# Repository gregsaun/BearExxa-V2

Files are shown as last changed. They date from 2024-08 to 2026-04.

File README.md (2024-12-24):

# BearExxa V2

## Table of contents
  1. [Introduction](#introduction)
  1. [Features](#features)
  1. [Disclaimer](#disclaimer)
  1. [Project Status](#project-status)
  1. [How To](#how-to)
  1. [Compatibility](#compatibility)
  1. [Bill Of Materials](#bill-of-materials)
  1. [Download](#download)
  1. [Print Settings](#print-settings)
  1. [Assembly Guide](#assembly-guide)
  1. [Configuration](#configuration)
  1. [Optional Parts](#optional-parts)
  1. [Official Kit](#official-kit)
  1. [Community And Help](#community-and-help)
  1. [Support My Work](#support-my-work)
  1. [Credits And Thank you](#credits-and-thank-you)
  1. [License](#license)

## Introduction 

This is the repository for the Bear EXtruder and X Axis version 2 (BearExxa V2). It improves Prusa MK2.5(S, S+) and MK3(S, S+) print quality, speed, reliability and serviceability. It's the [BearExxa V1](https://github.com/gregsaun/bear_extruder_and_x_axis) successor.

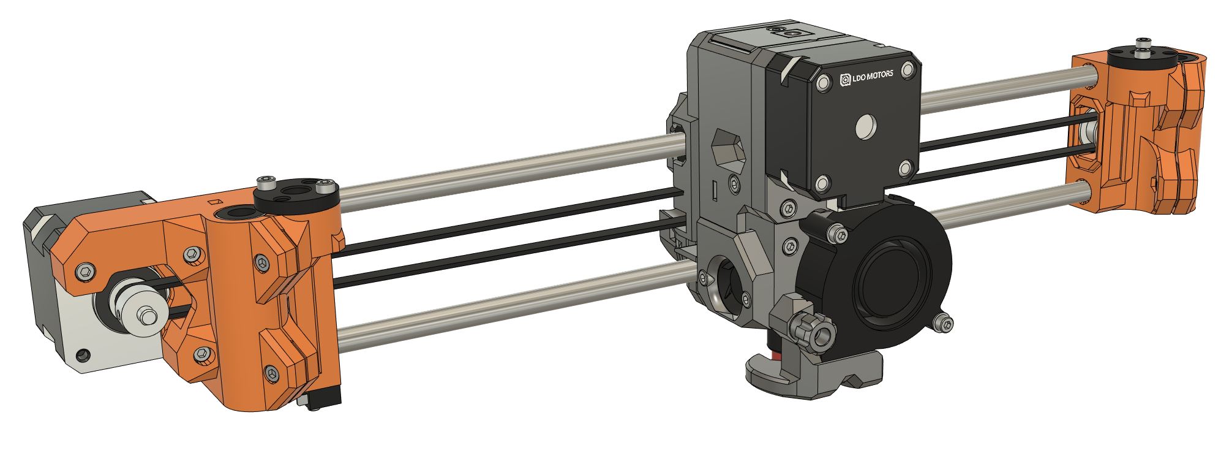
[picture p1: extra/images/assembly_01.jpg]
BearExxa V2 CAD assemnly


## Features

  - Compatible with stock Prusa MK2.5(S, S+) and MK3(S, S+) hardware as well as Bear frame
  - High print quality by solving both repetitive and random extrusion artifacts. Read our [Design Goals](extra/design_goals.md) for more information
  - High torque and cold extruder motor for the best reliability and print quality in all conditions
  - Light print head without compromising features
  - Short filament path
  - Built-in filament sensor
  - Very concentric extruder gearing
  - Stiffer X axis
  - Efficient belt tensioning system
  - E3D Revo hotend with quick swap nozzles
  - Support multicolour printing (MMU or ERCF)
  - Quick and easy to service
  - Optimized for high reliability
  - Improved cable management
  - Special attention to safety with CE compliant hardware and careful testing
  - No special tools, no crimping, no soldering and no difficult adjustments required during the assembly
  - Detailed assembly guides and documentation
  - Fully open source
 
:arrow_right: [Read our detailed Design Goals](extra/design_goals.md) to understand how we engineered those features.

## Disclaimer

This project is only to provide an alternative extruder and X axis to your Prusa printers. We are not related to Prusa Research. We cannot be taken responsible for any damages you may do by using this project nor any decision Prusa would take on you (e.g.: loosing warranty). This project is at your own risk.

## Project Status

Status: Beta 6 release done

This project is on hold for now. It's provided "as is" for any adventurous users interested in having a good extruder for their Prusa or Bear. The beta version of the BearExxa V2 provided here is fully functional and safe to use. The end goal is to provide a kit with all the parts and an improved stepper and hardware for better print quality and reliability (read our [Design Goals](extra/design_goals.md)).

## How To

How to print, build and start using the BearExxa V2:

1. Read the [Project Status](#project-status), [Disclaimer](#disclaimer) and [Compatibility](#compatibility) to make sure you agree to the limitations
2. Buy the official BearExxa v2 kit or gather the parts using the [BOM](#bill-of-materials)
3. Buy the filament according to the [Print Settings](#print-settings)
4. [Download](#download) the BearExxa V2 printed parts
5. Calibrate your filaments with our [Calibration Guide](https://guides.bear-lab.com/Guide/Extrusion+multiplier+and+filament+diameter/8)
6. Slice and print the parts according to the [Print Settings](#print-settings)
7. Follow the [Assembly Guide](#assembly-guide)
8. Enjoy your new extruder :)

## Compatibility

The BearExxa V2 is compatible with both Prusa MK2.5(S, S+) and MK3(S, S+). The original and Bear frames are both supported. The stock firmware can be used except for the initial calibration (self tests) for which we provide our own firmware.

:arrow_right: [Read all the compatibilities in details here](doc/compatibility.md)

## Bill Of Materials

The BOM includes the list of printed parts and hardware needed.

:arrow_right: [Read the BOM here](doc/bom.md)

## Download

Click here to download the printed parts for currently the recommended version (v2.0.0-beta.6):



## Print Settings

> [!WARNING]
> Follow the recommended print settings and [**calibrate your extrusion multiplier**](https://guides.bear-lab.com/Guide/Extrusion+multiplier+and+filament+diameter/8) before printing the parts.

:arrow_right: [Read the print settings here](doc/print_settings.md)

## Assembly Guide

For the current beta version we only provide a quick assembly guide.

:arrow_right: [Read the quick assembly guide here](doc/quick_assembly_guide/README.md)

## Configuration

Configurations needed for steppers and extruder values.

> [!NOTE]
> The configuration for the Original Prusa MK2.5(S, S+) and MK3(S, S+) is covered in the assembly guide.

➡️ [Find the configuration here](doc/config)

## Optional Parts

### Official optional parts

  - Multicolour with MMU or ERCF: [optional_parts/mmu_ercf](optional_parts/mmu_ercf)
  - Reverse Bowden: [optional_parts/reverse_bowden](optional_parts/reverse_bowden)
  - X-end tensioner for E3D toothed idler: [optional_parts/x_end_idler_tensioner_e3d](optional_parts/x_end_idler_tensioner_e3d)

Click here to download all optional parts (v2.0.0-beta.6):



### Community's optional parts

Find optional parts designed by the community at [guides.bear-lab.com/Wiki/community_optional_parts](https://guides.bear-lab.com/Wiki/community_optional_parts).

## Official Kit

> [!NOTE]
> The official kit is not yet available. Will be sold for the first RC release.

### What's included
  - Custom extruder motor by LDO Motors (read the [Design Goals](extra/design_goals.md) for more information)
  - Hotend fan with tachometer wire to pass Prusa firmware self tests and have extra safety
  - Quality toothed idler with dual bearings and correctly sized flanges
  - Wires and textile sleeve for a clean wiring
  - Bondtech hardware
  - All the necessary small hardware (screws, nuts, dowel pins, PTFE tube, etc.)

### What's not included
As the kit is dedicated to Original Prusa printers the kit doesn't include:
  - Z axis Lead screw nuts
  - X axis smooth rods
  - X and Z axis linear bearings
  - X axis motor
  - Filament sensor PCB, ball and magnets
  - SuperPinda (or Pinda v2)

To allow flexibility on the hotend side the kit doesn't include:
  - E3D Revo Micro heatsink
  - E3D Revo HeaterCore
  - E3D Revo nozzle

## Community And Help

- Bluesky: [@gregsaunier.bsky.social](https://bsky.app/profile/gregsaunier.bsky.social)
- Discord server "The 602 Wasteland": [discordapp.com/invite/hYUjSnW](https://discordapp.com/invite/hYUjSnW)
- GitHub: [github.com/gregsaun](https://github.com/gregsaun)
- Mastodon: [fosstodon.org/@bear_lab](https://fosstodon.org/@bear_lab)
- Patreon: [patreon.com/gregsaun](https://www.patreon.com/gregsaun)

Do not hesitate to ask if you have a question.

## Support My Work

The bear project is made possible thanks to its supporters. You can help via

- Patreon: [patreon.com/gregsaun](https://www.patreon.com/gregsaun)
- PayPal: [paypal.me/gregsaun](https://www.paypal.me/gregsaun)
- GitHub Sponsor: [github.com/sponsors/gregsaun](https://github.com/sponsors/gregsaun)

Massive thank you in advance :heart:

## Credits And Thank You

- The close help of Florian Däubler, [Paul_GD](https://github.com/PaulGD03), [Schaun Doe](https://www.printables.com/@ShaunDoe), Sleene and  [vertigo235](https://www.printables.com/@vertigo235_33)
- All [my Patreons](https://www.patreon.com/gregsaun), it would have been impossible without their help
- [LDO Motors](https://ldomotors.com) for their continuous and precious support and sponsoring. LDO will manufacture the official kit for the final release with a custom stepper
- [E3D Online](https://e3d-online.com) for providing free hotends for development
- [Bondtech](https://www.bondtech.se) for providing free IDGA gears for development
- The [fan duct knob](https://www.printables.com/model/113157-bear-extruder-v1-fan-duct-knob) by Amelia Marie Collins
- [René Jurack](https://rene-jurack.de) for helping me on CFD simulation for the nozzle fan duct
- [Credits from BearExxa V1](https://github.com/gregsaun/bear_extruder_and_x_axis?tab=readme-ov-file#credit-and-inspiration) related to X Ends: Vecko Kojchevski, Arnaud Rousseau and Jon Madden
- Keith Bennett for making the [Prusa AIO firmware](https://github.com/thisiskeithb/PrusaAIO) compatible
- [PoiTEE](https://x.com/PoiTEE) for the great talks and testing
- [FilamentFrenzy](https://x.com/FilamentFrenzy) for having tested and make noise for an early version
- Prusa Research for their MK2.5S and MK3S designs
- Adrian Bowyer for inventing [RepRap](https://reprap.org)

Thank you everyone ❤️

## License

The Bear EXtruder and X Axis v2 (BearExxa V2) is an open-source hardware project created from scratch by Grégoire Saunier with help and inspiration from the people and companies listed under "Credits and Thank You" as well as contributions linked to this repository.

All texts, images, PDF files and animations in this repository are licensed under the terms of the CC-BY-SA 4.0 license. The full license text of CC-BY-SA 4.0 is available in this repository at [`./LICENSE-CC-BY-SA-4.0`](./LICENSE-CC-BY-SA-4.0). Read more about this license [here](https://creativecommons.org/licenses/by-sa/4.0/).

All G-code files in this repository are licensed under the terms of the MIT license. The full license text of MIT is available in this repository at [`./LICENSE-MIT`](./LICENSE-MIT). Read more about this license [here](https://opensource.org/license/MIT).

All content in this repository, except for texts, images, PDF files, animations and G-code files is licensed under the terms of the CERN-OHL-P v2 license. The full license text of CERN-OHL-P v2 is available in this repository at [`./LICENSE`](./LICENSE). Read more about this license [here](https://cern-ohl.web.cern.ch/).

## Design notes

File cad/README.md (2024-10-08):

# BearExxa V2

## CAD

> [!IMPORTANT]
>The X end idler and its tensioner are a working progress in these CAD files. They are **currently** not compatible with the previous X end idler and tensioner. The STL files exported into `../printed_parts/stl` are a copy of the Bear extruder V1 X ends ([source files of V1](https://github.com/gregsaun/bear_extruder_and_x_axis/tree/master/source)). The future revisions will make them compatible with the V1.

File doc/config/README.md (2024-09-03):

# BearExxa V2

## Configuration

### Original Prusa MK2.5(S, S+) and MK3(S, S+)

Due to the gear ratio of the BearExxa V2 we need to configure the estep and microstepping values.

➡️ [Download the config files `prusa_original/config_prusa_original_bearexxav2_beta.zip`](./prusa_original/config_prusa_original_bearexxav2_beta.zip).

In the ZIP you will find the following files:
  * `bearexxa2_config.gcode`: Use this file to setup microstepping and estep.
  * `reset_config_to_prusa_mk2.5-2.5s-3-3s.gcode`: Use this file to reset changes previously applied for BearExxa v2 to stock Prusa config.

### Prusa AIO firmware (Marlin 2.x)

*to do*

### Klipper

*to do*

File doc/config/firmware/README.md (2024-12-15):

# BearExxa V2

## Firmware Configuration

### Table of Contents

  1. [Original Prusa MK2.5(S, S+) and MK3(S, S+)](#original-prusa-mk25s-s-and-mk3s-s)
  1. [Prusa AIO firmware (Marlin 2.x)](#prusa-aio-firmware-marlin-2x)
  1. [Klipper](#klipper)
  1. [Generic](#generic)

### Original Prusa MK2.5(S, S+) and MK3(S, S+)

Due to the gear ratio of the BearExxa V2 we need to configure the estep and microstepping values.

In the folder [prusa_original](prusa_original) you will find the following files:
  - `bearexxa2_config.gcode`: Use this file to setup microstepping and estep.
  - `reset_config_to_prusa_mk2.5-2.5s-3-3s.gcode`: Use this file to reset changes previously applied for BearExxa v2 to stock Prusa config.

> [!WARNING]
> These GCODE files only applyto Prusa firmware and **not** to Prusa AIO or Klipper.

### Prusa AIO firmware (Marlin 2.x)

BearExya V2 is officially supported by the Prusa AIO firmware. Please refer to the [GitHub](https://github.com/thisiskeithb/PrusaAIO) and [wiki](https://github.com/thisiskeithb/PrusaAIO/wiki) for the configuration.

### Klipper

#### Extruder
```yaml
[extruder]
rotation_distance: 22.616
microsteps: 32
full_steps_per_rotation: 200
gear_ratio: 2.94:1
sensor_type: ATC Semitec 104NT-4-R025H42G
```
> [!WARNING]
> These are not complete configurations. Please adjust your configuration to reflect the values below.

#### Extruder motor driver
For TMC2209 and TMC2130 using the Klipper extension  [klipper_tmc_autotune](https://github.com/andrewmcgr/klipper_tmc_autotune).
```yaml
run_current: .42
```

#### X axis motor driver
For TMC2209 and TMC2130 using the Klipper extension  [klipper_tmc_autotune](https://github.com/andrewmcgr/klipper_tmc_autotune).
```yaml
run_current: .5
```
> [!NOTE]
> Using the TMC Autotune extension is not a requirement, and these motor currents are only a recommendation.
> 
> Please adjust these values according to the motors you are using, ideally >50% and <80% of the rated current.

### Generic

#### Extruder

```
Number of steps per motor rotation: 200
Microsteps: 32
Gear Ratio: 2.94:1
Effective hobb gear diameter: 7.22mm
Running current: 420mA RMS
Holding current: 420mA RMS
Interpolation: true
Hotend thermistor: Semitec 104NT-4-R025H42G 
```

#### X axis

```
Number of steps per motor rotation: 200
Microsteps: 16
Running current: 500mA RMS
Holding current: 300mA RMS
Interpolation: true
 ```

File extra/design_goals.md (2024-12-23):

# BearExxa V2

## Design Goals

### Table of contents

1. [Introduction](#introduction)
1. [Print quality](#print-quality)
1. [Reliability](#reliability)
1. [Weight, rigidity and speed](#weight-rigidity-and-speed)
1. [Custom extruder motor](#custom-extruder-motor)
1. [Serviceability and maintenance](#serviceability-and-maintenance)
1. [Safety](#safety)
1. [FAQ](#faq)

### Introduction

The main goals of the BearExxa V2 are to use a better hotend and geared extruder to improve the print quality, reliability, serviceability, precision, speed and to solve inconsistent extrusion issue (602 issue).

There are several ways to achieve this and it's a question of what compromises you do and how you test things. In this page we describe our design process and the goals we have set to achieve the BearExxa V2.

BearExxa V2 assembly

### Print quality

This extruder improves print quality by using a geared extruder, a well engineered hotend and several thoroughly designed features. Here is how we have cured the 602 issue (inconsistent extrusion issue) as well as improving even further the print quality:

#### Random extrusion artifacts and precision

The first crucial aspect to get quality prints is to handle the filament precisely and rigidly down to the melt zone.

To achieve this we use a perfectly aligned, short and smooth filament path to reduce any potential friction. The path is shorter than on the original MK3(S, S+).

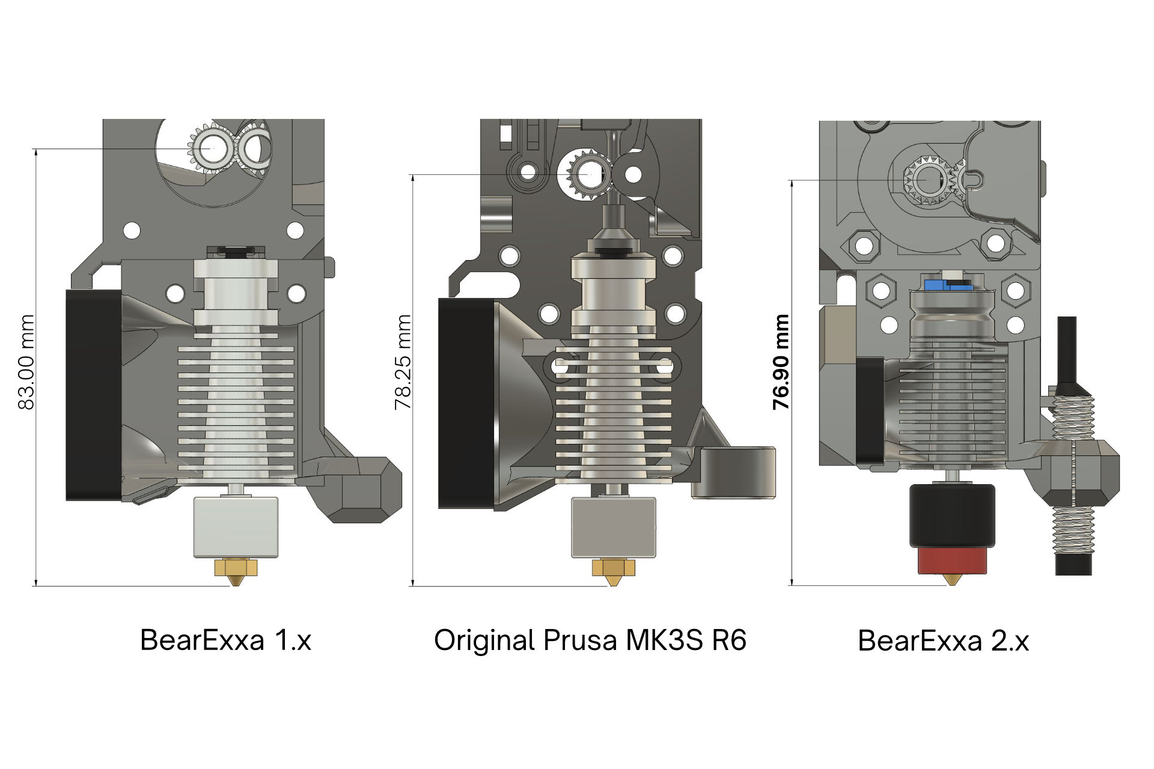
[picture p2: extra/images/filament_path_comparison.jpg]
BearExxa V2 filament path length comparison


We use a NEMA 17 pancake motor to keep the hobb gears and its cavity as cold as possible, even on long PLA prints in enclosure with doors closed. This helps to keep the filament as rigid as possible before the hotend and so increase precision.

We are also using the small set of the dual Bondtech hobb gears as its small diameter allows to catch the filament exiting the hobb gears closer than with a larger diameter. It reduces chances for the filament to go out of the path like it could happen with flexible filaments.

Then comes the hotend, we chose the E3D Revo because we have observed that it's particularly good at reducing random artifacts on perimeters compared to some competitors we have evaluated or tested. But it needs a good control of the filament on both cold and hot sides, so we took care of the airflow and thermal management to get a very sharp thermal transition in the heatbreak. This is achieved with the Revo Micro heatsink, a properly sized fan and a careful aiflow's management.

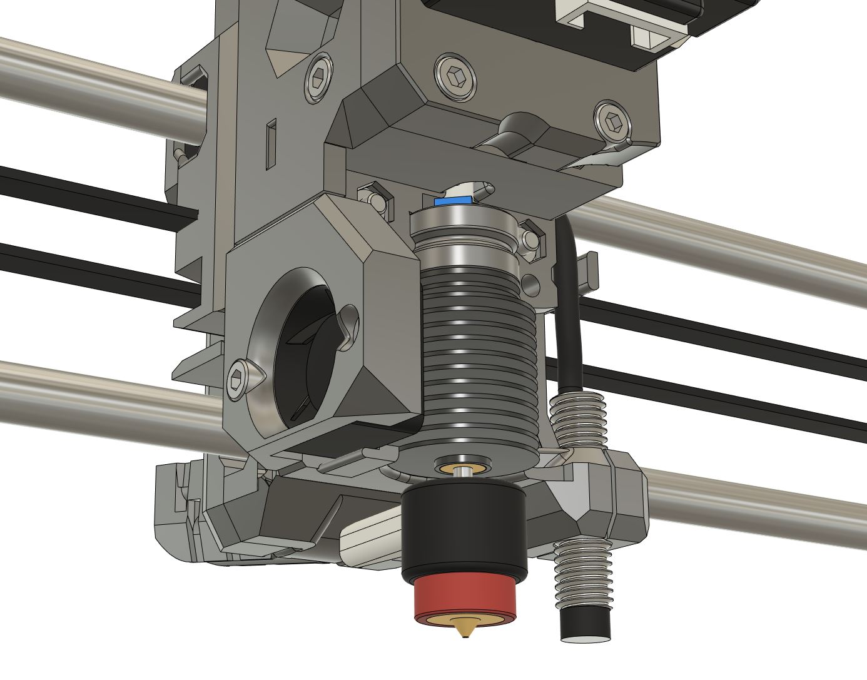
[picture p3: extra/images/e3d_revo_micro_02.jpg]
BearExxa V2 Hotend and its fan


Furthermore, we made sure to have a free space right below the heatsink to cool this side as well with the movements of the tool head. It's important because the bottom side of the heatsink is where it matter the most for the heatbreak.

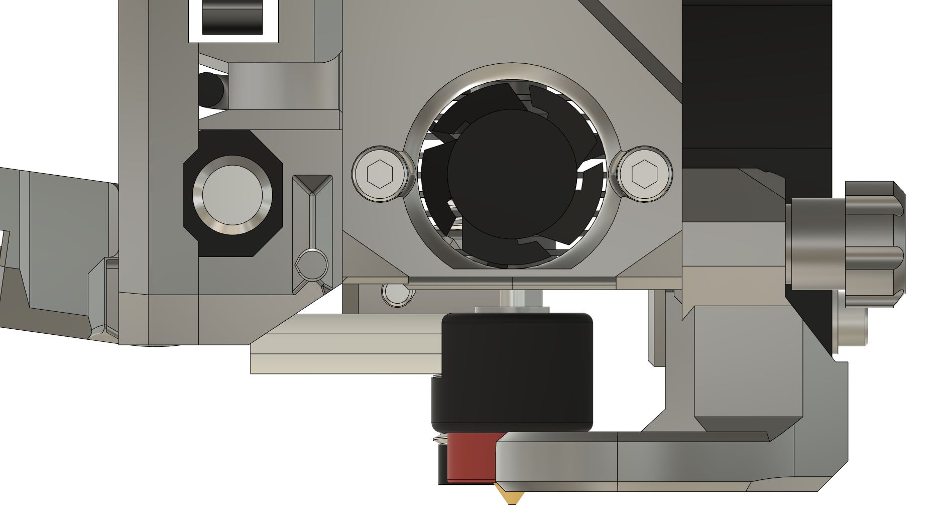
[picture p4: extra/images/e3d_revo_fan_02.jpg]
BearExxa V2 hotend cooling


All these features **improve random extrusion artifacts and increase the accuracy** of your prints.

#### Repetitive extrusion artifacts

The extruder uses a gear ratio of 3:1 (with beta release) or almost 4:1 (with the future final release). 

We took care of using appropriate teeth numbers to have a smooth rotation and to reduce the wear on the teeth (e.g. coprime number of teeth, hardened teeth, large surface of contact). We believe that the print quality should be the same even after many hours of use!

The custom motor has enough torque to not make the motor's steps more visible when the pressure increases in the hotend due to non-optimal settings or other small issues (wider extrusion, partial clog, too high flow rate, ...). This custom motor has a very concentric gear that will reduce variations in the rotation. For the final release we are also planning to use the all in one piece Bondtech shaft and hobb gear (IDGA) to once again reduce the variations.

All those features **improve the so called "moiré pattern" (also called basket wave or wood grain pattern)** or, in other words, the repetitive extrusion artifacts.

#### Single vs dual hobb gears

Finally, we have made several tests comparing single vs dual gears and we couldn't see a difference. We also asked the Bear community to test on their side and they had the same conclusion.

We understand there is a gear meshing issue but we think it can potentially only happen during retraction or maybe the artifacts are too small to be visible.

We also think that some of our design decisions are potentially helping to minimise this issue (rigid extruder cavity, tight tolerances to align the gears, good amount of tension with visible indicator, precise filament path, etc.).

We may later provide a mod to use a single gear for making your own conclusion. We are keeping an eye on this topic and for now we haven't seen good enough testing proving there is a noticeable difference.

### Reliability

Reliability is a strong goal of this extruder. We use a NEMA 17 pancake motor to keep the hobb gears and the extruder cavity as cold as possible during extensive PLA prints in enclosure (door closed).

After multiple testing with belts and planetary gearboxes we found that a single stage of spur gears is the best compromise. It's light, easy to assemble and has a very low part count, which means less parts can fail.

We use the Bondtech gear shaft and hobb gears, but we replaced the original bearings by larger ones to increase lifespan (and smoothness).

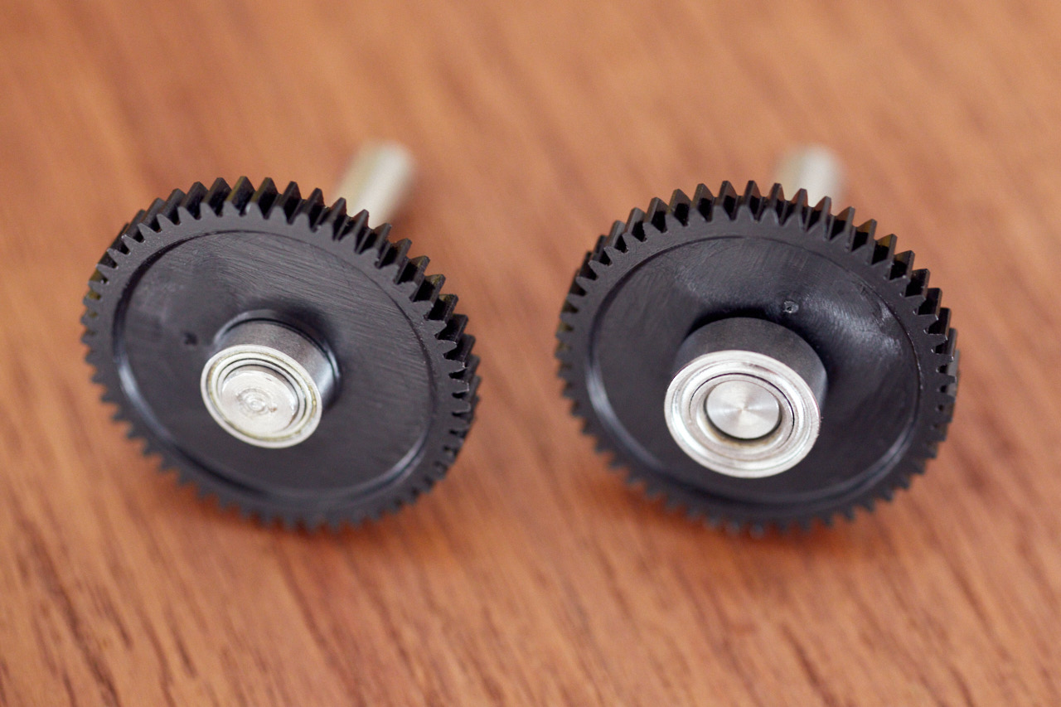
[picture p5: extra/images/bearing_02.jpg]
BearExxa V2 bearings


We use the E3D Revo Micro hotend for its professional support and compliances with worldwide regulations. We optimized the hotend airflow for the best heatbreak performance possible, low noise and to avoid grabbing tiny hairs (strings).

We placed the nozzle fan blower in vertical to maximise the lifespan of its bearings, to not get warmer air when the extruder is close to the bed and, once again, to avoid getting strings in the fan blades.

Unlike the Original Prusa MK3S and MK3S+ extruder, the filament path is in one piece to avoid a potential misalignment during assembly that would affect its smoothness. It's also shorter than the original Prusa extruder.

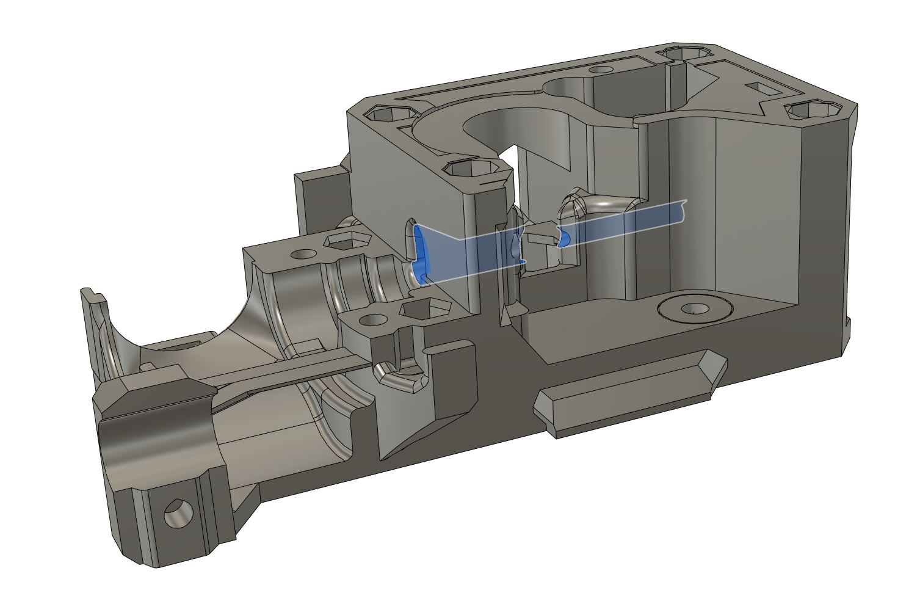
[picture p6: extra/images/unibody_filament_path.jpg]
BearExxa V2 unibody filament path


Every printed parts and features have been tested carefully. When rigidity or brittleness could be affected we made internal reinforcements within the infill to reduce any risks.

We also make sure that no special adjustments or tools are required during the assembly and maintenance. With the final release we will provide detailed assembly guide, as we always do, to avoid any potential assembly issues.

### Weight, rigidity and speed

Despite a larger motor than what's commonly used these days, a lot of work have been implemented to make the extruder as light as possible, even lighter than some extruders widely used in the community! Let's dive into how we achieved this.

First, it's important to remember that a bed slinger printer doesn't have to carry the weight of the gantry like on a CoreXY machine, which means the mass in motion is lighter than we could first think. However, obviously, the bed is heavier and will be the bottleneck.

On our design, we reduced the weight by using a light and small hotend (including the fan), using a single stage spur gears instead of a heavier planetary gearbox, lowering the number of screws, using small hobb gears, carefully selecting the hardware, not adding extra useless features and designing a compact body.

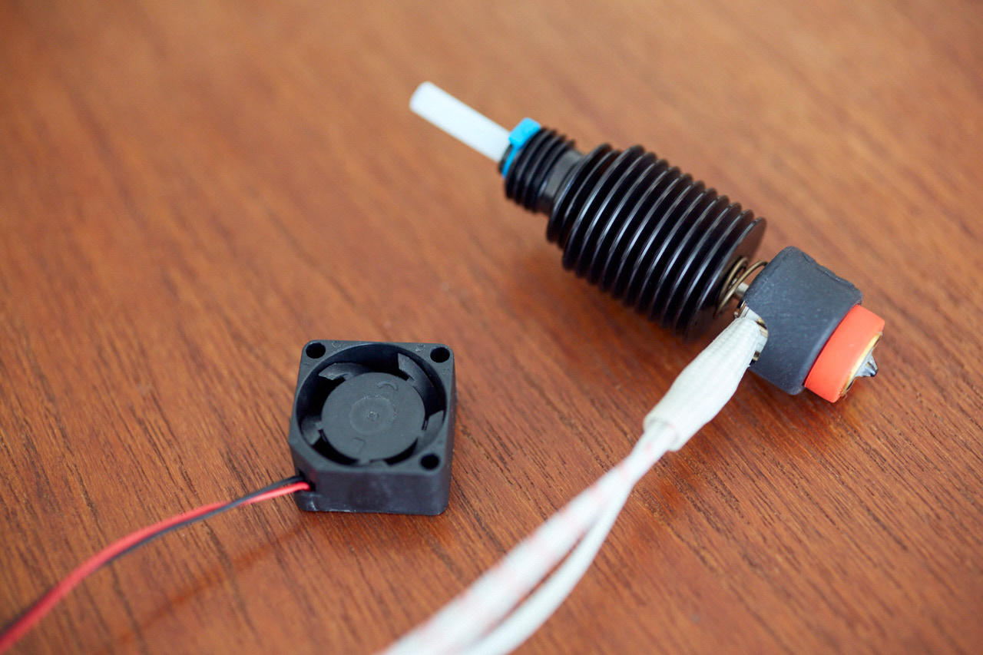
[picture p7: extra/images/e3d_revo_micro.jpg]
E3D Revo Micro and its fan


As you can see we took care of every weight reduction that matters but we didn't stop there. The X axis is stiffer thanks to several design startegies: we use clamps on the Z axis bearings, X motor is closer to the Z axis, the belt tensioner is stiff and we optimized how deep the smooth rods are inserted in the X ends.

### Custom extruder motor

> [!WARNING]
> Not for the Beta release, will only be for RC and final releases.

The final release will use a custom extruder motor by LDO Motors. It was a difficult choice to take as we want to be as open hardware as possible but the improvements are significant.

This custom motor uses a carefully selected gear ratio (almost 4:1) for smoother print quality and to minimise the teeth wear (e.g. coprime number of teeth, hardened teeth, large surface of contact). It has a special construction to make the motor gear very concentric and so to reduce extrusion variations. It also helps to reduce the total weight.

The back of the motor is almost empty inside, it has been made thicker to accommodate a connector. Like this, we reduce the maintenance time and so be quicker to restart printing.

Finally, the motor specs are optimized for original Prusa printers to provide a safe amount of torque on all occasions as well as keeping the motor cold for long PLA prints in enclosure. We chose a motor that has just enough torque to grind the filament in case of a blockage. This is to avoid problems where the spool or the filament path has lots of friction (didn't we all have a failed print due to this?), to fight slightly non-optimal settings that could force on the hotend's flow, to resolve a small heat creep and to ensure manufacturing tolerances are covered (including the precision of your printed parts). With higher torque we could also imagine to later automate things like cold pulls. We believe that a finished print is always better than a failed one that will be sent to trash (even if the quality is a bit below what you wanted to achieve), so high torque was a crucial feature for us.

### Serviceability and maintenance

Thanks to the E3D Revo ecosystem you can swap nozzles with two fingers in a few seconds. And to make this even easier, you can remove the hotend fan duct with a thumb screw.

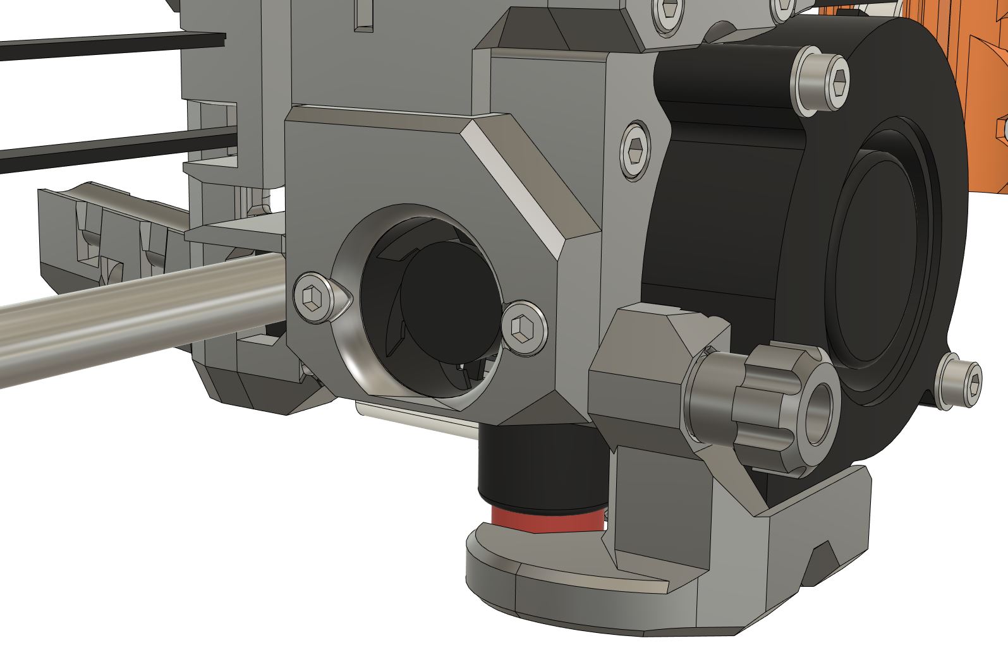
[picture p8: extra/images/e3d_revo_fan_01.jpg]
BearExxaV2 Thumb screw nozzle fan duct shroud


The hobb gear tension has a visual adjustment for the nominal tension.

The belt tensioner is easy to use and has a long adjustment range.

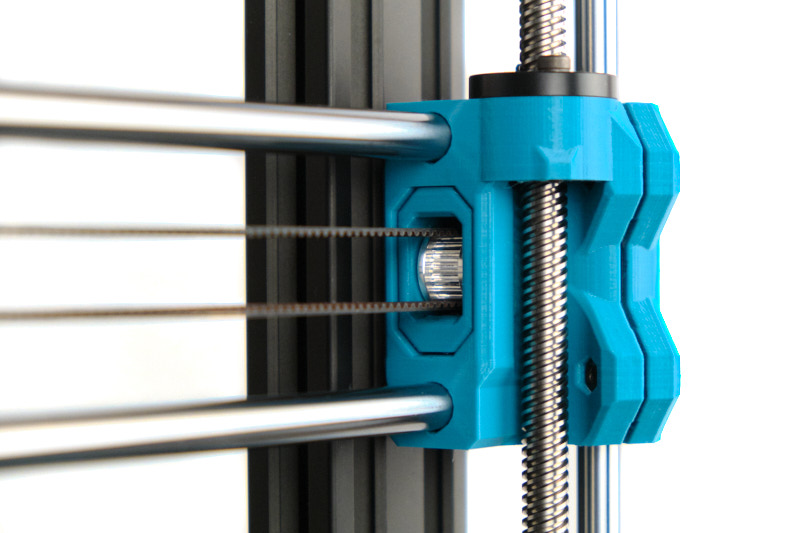
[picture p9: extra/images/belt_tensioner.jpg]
BearExxa V2 belt tensioner


You only need to remove 4 screws and unplug the motor cable to access the gearing, the hobb gears, the filament sensor and the top of the PTFE tube. Cleaning and maintenance are a breeze and quick.

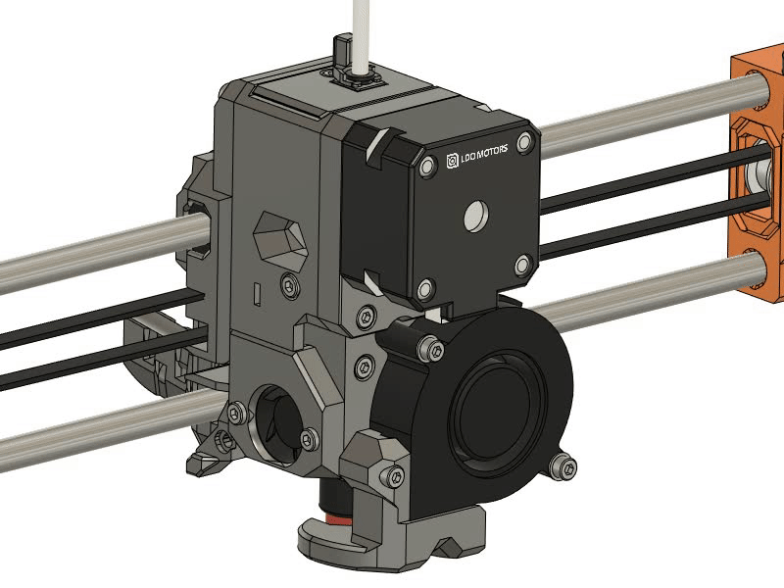
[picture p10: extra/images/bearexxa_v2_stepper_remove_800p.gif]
BearExxa V2 removing motor anf gears


We invented a self tightening groove mount that blocks the rotation of the Revo Micro heatsink thread. Like this there are zero chances to unscrew the heatsink when swapping nozzles.

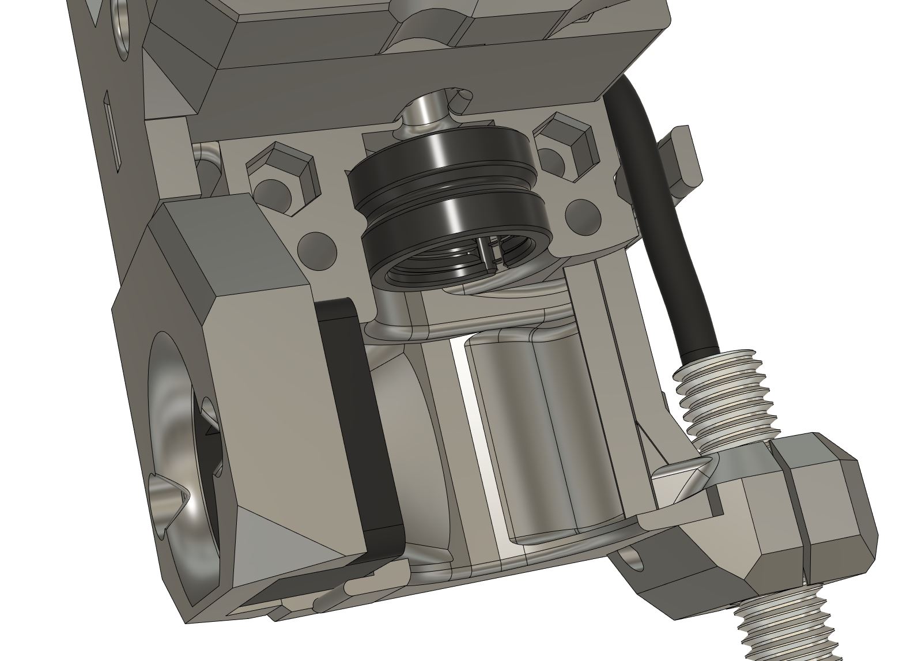
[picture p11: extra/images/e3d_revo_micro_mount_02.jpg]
E3D Revo self tightening groove mount


The back of the X carriage is made into two parts to access all the wiring and the belt freely.

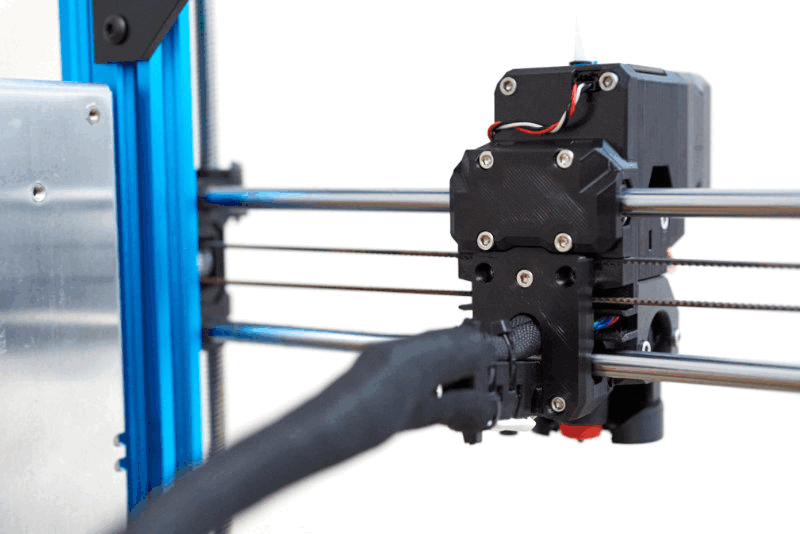
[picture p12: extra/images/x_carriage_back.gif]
BearExxa V2 X carriage back


### Safety

We can be very picky when it comes to the safety of our project, especially as it's DIY and open source. A 3D printer is a machine melting flammable plastic for hours and hours, it must be safe!

We chose the E3D Revo hotend for its worldwide compliances (CE, UKCA RoHS, etc.). It's also particularly interesting that the  Revo is using a PTC heater which offers an extra safety in case of thermal runaway. Our design ensure that the wire harness of the HeaterCore is kept straight and that no wires have sharp angle. No crimping, cutting or soldering is required. The hotend fan that will come with the final kit will have the tachometer wire to detect a fan failure.

We recommend PETG for the extruder parts because its a safe filament to use. It doesn't burn easily and do not release too much nasty fumes. The extruder has obviously been tested to support the temperature for long prints.

We provide detailed documentation, assembly guides and many other helps. Like this you reduce as much as possible the issues during assembly, printing, maintenance and have many resources in case of problems. If it's not enough we are here to provide support, there are no bad questions.

We only recommend genuine Bondtech, E3D, LDO Motors, and Prusa hardware for the best safety and support possible. We will provide an official kit that has been carefully designed and controlled (manufactured by LDO Motors). Using clone parts from another manufacturer is a risk of incompatibility, reliablitiy, legality and even fire.

### FAQ

#### Why don't you use heat inserts?
Hex or square nuts have a stronger pulling resistance than heat insert. We use carefully selected clearances to make sure the hex nuts will not move from their pocket. The nuts also take less place than heat insert. We can also simulate a lock nut by making the screw hole in the plastic a little bit smaller. It's easier to remove them from an older part to transfer them to a new one. Finally, no special tool is required.

#### Why the nozzle fan blower is in vertical and not angled like Prusa does?
It's to increase the lifespan of its bearings, to not get warmer air when we are close to the bed and to not grab strings with the fan blades. The nozzle fan duct is optimized for the 90° angle and perform better than the Original MK3(S, S+) according to our tests.

#### Why do you recommend PETG for the parts?
PETG has an excellent layer bonding, is easy to print, has high precision due to low shrinkage, is kind of semi fire retardant and produces less nasty fumes than styrene based filaments. Its temperature resistance is more toward printing PLA or PETG parts (even in enclosure) which are the most used filaments in the community. If you are an advanced user that want to print higher temperature material we recommend to use ABS, ASA or PC (and compensate for the shrinkage).

> [!CAUTION]
> We highly recommend to avoid high flow filaments (worse material properties as non high flow) as well as glass fiber or carbon fiber filaments ([potentially carcinogenic](https://hackaday.com/2024/08/07/on-carbon-fiber-types-and-their-carcinogenic-risks/)). You must ventilate your room and filter your enclosure (HEPA + activated carbon) if you print styrene based filament like ABS, ASA or PC.

#### Why don't you use a smaller extruder motor?
We have explained the reason in details in the sections "Print quality", "Reliability" and "Weight, rigidity and speed".

The extra weight is compensated by other lighter parts, low hardware count and an overall compact design. Also, it would be very hard to see a print quality improvement with a lighter motor because, on a bed slinger, we are only moving the extruder (unlike CoreXY which also moves the gantry) and the bed is the heaviest part. 

Furthermore, a larger motor can run colder and so improves print quality and reliability of a long PLA print in an enclosure (door closed). We can also have higher torque and increase the gears' lifespan, which both increase reliability and reduce maintenance.

#### Why do you use the Revo Micro heatsink and not the Revo Voron heatsink?
The Revo Micro heatsink has slightly more surface in contact with the airflow, especially when used with a smaller and lighter fan. The round shape is also easier to optimize for optimal airflow. The screw mount may sound like it may rotate but we did a self tightening system that avoid this to happen.

#### Why don't you officially support other hotends?
Using a single hotend allow us to optimize a lot of design's aspects like size, weight, filament path, etc. Supporting a single hotend means we can also have a more reliable testing and provide quality support. Finally, we choose E3D-Online Ltd. because their products have all the worldwide safety compliances, they provide a full ecosystem, they do deep research and engineering on how a hotend works and they have a professional support for their customers.

#### Why don't you use the Bondtech IDGA gear?
We are well aware of the IDGA benefits. We have actually talked about it with Bondtech engineers several years ago when the Bondtech Prusa extruder was introduced and more recently for the development of the IDGA. We also thought to design our own gears as we see improvements but making a custom motor was already a big step.

When we released the beta BearExxa V2, the IDGA gear was unfortunately not available and so it's not supported yet. We will make the final version compatible with BMG IDGA or OEM IDGA (we don't know which one is best yet). However, we can guarantee that even without the IDGA the print quality is a big step over BearExxa V1 and 602 pattern (moiré, wood grain. inconsistency) has been drastically reduced.

#### Would it be possible to use a stronger fan like the one on the MK4S?
Yes we want to work on this but at the moment we focus on stock Prusa MK3(S, S+) hardware.

#### Do you support MK3.5S?
We don't know yet but it might be possible. We are [looking for help](https://github.com/gregsaun/BearExxa-V2/issues/1) if you want to try the adventure.

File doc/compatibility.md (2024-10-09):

# BearExxa V2

## Compatibility

### Frame

The BearExxa V2 is compatible with both Original and Bear frames of Prusa MK2.5(S, S+) and MK3(S, S+).

### Firmware

#### Original Prusa firmware

The stock Prusa firmware is supported with the following conditions:
- Self tests and XYZ calibrations need to be done with the [Bear calibration firmware](https://github.com/bear-lab-3d/Prusa-Firmware/releases/latest). All the normal printing routines, including first layer calibrations, will work as normal with the stock Prusa firmware. Note that you can also safely use the Bear calibration firmware for printing daily
- The thermal algorithm for the hotend introduced in the very latest Prusa firmwares can sometimes cause issues with the fast Revo heating. There are commands to use the previous standard method (we provide the documentation to do it)
- For the **beta** release only: you will need to disable fan checks for prints and temporarily plug the stock hotend fan during self test procedure. The final version will be sold as a kit with a compatible fan and this will not be needed anymore

> [!IMPORTANT]
> This is the firmware we recommend for the best safeties and to keep all the functionalities provided by the Prusa firmware. We can provide full support to our customers with this firmware.

The final release of BearExxa V2 will not disable or affect any safeties from the original Prusa firmware (and same applies for the Bear calibration firmware). The E3D Revo hotend is actually providing an extra safety in case of thermal runaway compared to the E3D V6 used in the Original Prusa.

#### Other firmwares

> [!IMPORTANT]
> We can only provide limited support to these firmwares.

The BearExxa V2 is also compatible with the [Prusa AIO Marlin 2.x firmware](https://github.com/thisiskeithb/PrusaAIO). This firmware can run on some 32b boards. Thanks Keith for this impressive work!

We will provide main Klipper parameters for the final version of BearExxa V2.

### MMU and ERCF

The extruder is designed from scratch to be capable of multicolour printing with systems like Prusa MMU or ERCF.  You can find more information in the [optional parts](/README.md#optional-parts).

### BearExxa V1, BearMera and Bondtech Bear X axis

The X axis of BearExxa V1, BearMera (E3D Hemera) and Bear X axis and carriage for Prusa original Bondtech are all 100% compatible.

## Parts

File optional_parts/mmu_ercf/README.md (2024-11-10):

# BearExxa V2

## MMU ERCF adapter

### Introduction

To make your BearExxa V2 capable of printing in multicolour with Prusa MMU or [ERCF by EtteGit](https://github.com/EtteGit/EnragedRabbitProject).

The PTFE mount on the extruder is available in two options:
  - Reuse the Prusa hardware (brass insert and Festo coupling). Note that the brass insert is easy to remove in general
  - Use the E3D collet system for a lighter and the PTFE pass through system

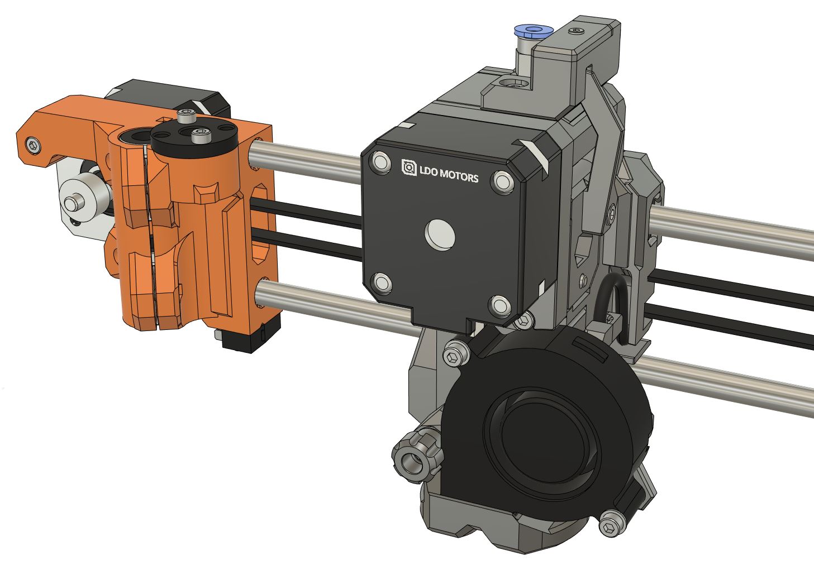
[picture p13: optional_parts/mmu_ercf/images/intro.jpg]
Introduction Bearexxa V2 MMU intro

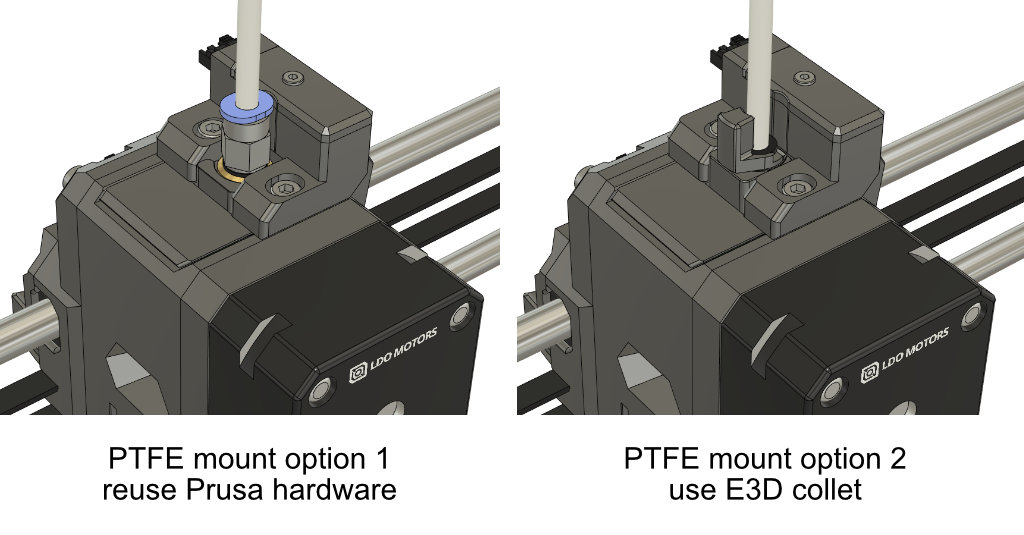
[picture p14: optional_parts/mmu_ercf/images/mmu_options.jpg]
Introduction Bearexxa V2 MMU PTFE options


### Bill of Materials

| Part | Quantity | Comment | Link |
|---|:---:|---|---|
| Prusa MMU or ERCF unit | 1 | | |
| M2x8 (ISO 4762) | 1 | | |
| M3x10 (ISO 4762) | 1 | | |
| M3x14 (ISO 4762) | 1 | | |
| M3x18 (ISO 4762) | 1 | | |
| M3 square nut (DIN 562) | 1 | | |
| M3 hex nut (ISO 4032) | 1 | | |
| E3D bowden collet for metal 1.75mm | 1 | Only for PTFE mount option 2 | [E3D link](https://e3d-online.com/products/embedded-bowden-coupling-for-metal) or [Prusa link](https://www.prusa3d.com/product/heatsink-collet/) |
| Prusa filament sensor | 1 | Comes with your Prusa MK3S (or S+) printer | [Prusa link](https://www.prusa3d.com/product/ir-filament-sensor/) |
| Prusa filament cable | 1 | Comes with your Prusa MK3S (or S+) printer | [Prusa link](https://www.prusa3d.com/product/filament-sensor-einsy-cable/) |
| Prusa 10x6x2 magnet | 1 | Comes with your Prusa MK3S (or S+) printer | [Prusa link](https://www.prusa3d.com/product/set-of-magnets-mk2-5s-mk3-s/) |
| Prusa 20x6x2 magnet | 1 | Comes with your Prusa MK3S (or S+) printer | [Prusa link](https://www.prusa3d.com/product/set-of-magnets-mk2-5s-mk3-s/) |
| Prusa 7mm steel ball | 1 | Comes with your Prusa MK3S (or S+) printer |  |

### Printed parts

Download all optional parts with the button at [Repo Homepage -> Optional Parts -> Official optional parts](/README.md#official-optional-parts)

### Print settings

> [!WARNING]
> The parts have been designed and tested with the parameters below and it is important to follow them to avoid issues like part cracking, bad bridging, not enough stiffness or wrong tolerances. You must [**calibrate your extrusion multiplier**](https://guides.bear-lab.com/Guide/Extrusion+multiplier+and+filament+diameter/8?lang=en) before printing the parts.

You can use the default PrusaSlicer print profile *0.20mm QUALITY @MK3* with 4 perimeters and 5 tops/bottoms layers and 20% infill. Otherwise, here are the parameters we recommend:

  - Slicer : PrusaSlicer
  - Nozzle size : 0.4mm
  - Layer height : 0.2mm
  - Infill : 20% Cubic or 20% Gyroid
  - Number of perimeters : 4
  - Number of top/bottom layers : 5
  - Default extrusion width : 0.45mm
  - Perimeters width : 0.45mm
  - External perimeters width : 0.45mm
  - Support : No
  - Brim : No
  - Detect thin walls : No

### Filament type

The parts are designed for PETG and this is what we recommend. Please consider recycled filament and cardboard spool or masterspool. If you are using a different filament material you will need to account for the shrinkage in XY plane directly in the slicer.

| Part | Quantity | Filament |  Color  | Comment |
|---|:---:|:---:|:---:|---|
| e_fs_adapter_mmu2s_prusa | 1 | PETG |  Any | For PTFE mount option 1 |
| e_fs_adapter_mmu2s_e3d | 1 | PETG |  Any | For PTFE mount option 2 |
| e_fs_adapter_mmu2s_e3d_clip. | 1 | PETG |  Any | For PTFE mount option 2 |
| e_fs_chimney_cover_mmu2s | 1 | PETG |  Black  | |
| e_fs_chimney_mmu2s | 1 | PETG |  Black  | |
| e_fs_cover_mmu2s | 1 | PETG |  Any | |
| e_fs_lever_mmu2s | 1 | PETG |  Black  | |
| e_tensioner_mmu2s | 1 | PETG |  Any | |

Note 1: Avoid eSUN PETG as some user reported that it might not block IR signal correctly. No other PETG have been reported to have this issue yet.

### Assembly

Read the [assembly guide here](assembly_guide/mmu_assembly_guide.pdf)

### CAD Files

The native CAD (Fusion) and STEP files are available at [`/cad/optional_parts`](/cad/optional_parts)

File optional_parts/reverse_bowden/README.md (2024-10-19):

# BearExxa V2

## Reverse bowden adapter

### Introduction

Reverse bowden has the advantage to reduce vibration and tension from the spool holder. It is also useful to guide the filament if the spool holder is not on top of the frame.

The extruder adapter is available in two options:
  - no collet where PTFE is just pushed into the hole (enough holding in most cases, easy to use and light)
  - E3D collet when strong PTFE holding is needed

The frame mount is available in two versions: standard or angled.

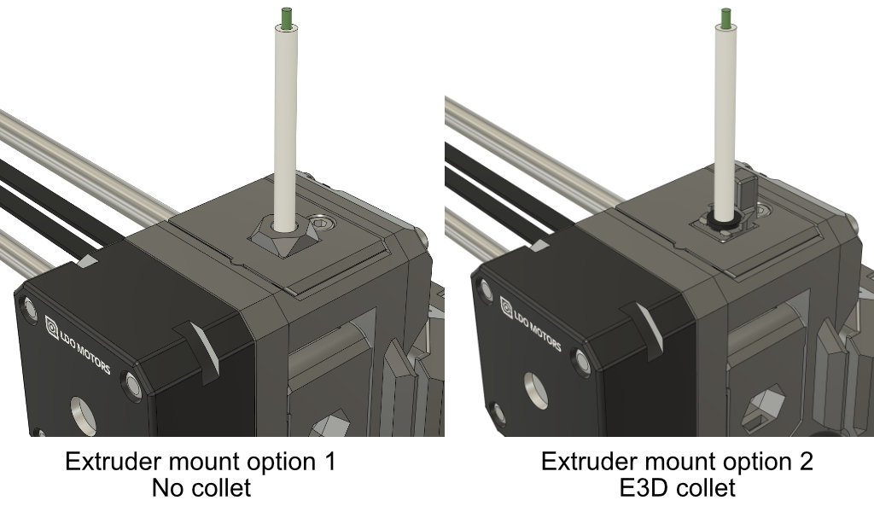
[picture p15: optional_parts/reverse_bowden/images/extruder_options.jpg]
Introduction reverse bowden

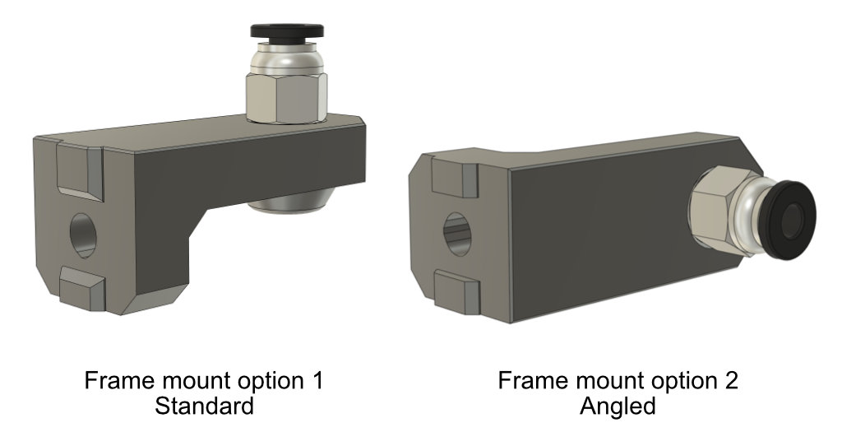
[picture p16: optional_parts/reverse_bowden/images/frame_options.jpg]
Introduction reverse bowden


### Bill of Materials

| Part | Quantity | Comment | Link |
|---|:---:|---|---|
| PTFE tube 4x2mm | 1 | | |
| E3D bowden collet for metal 1.75mm | 1 | Only for extruder option 2 | [E3D store](https://e3d-online.com/products/embedded-bowden-coupling-for-metal) |
| PC4-M10 fitting | 2 | For the frame mount |  |

### Printed parts

Download all optional parts with the button at [Repo Homepage -> Optional Parts -> Official optional parts](/README.md#official-optional-parts)

## Print settings

> [!WARNING]
> The parts have been designed and tested with the parameters below and it is important to follow them to avoid issues like part cracking, bad bridging, not enough stiffness or wrong tolerances. You must [**calibrate your extrusion multiplier**](https://guides.bear-lab.com/Guide/Extrusion+multiplier+and+filament+diameter/8?lang=en) before printing the parts.

You can use the default PrusaSlicer print profile *0.20mm QUALITY @MK3* with 4 perimeters and 5 tops/bottoms layers and 20% infill. Otherwise, here are the parameters we recommend:

  - Slicer : PrusaSlicer
  - Nozzle size : 0.4mm
  - Layer height : 0.2mm
  - Infill : 20% Cubic or 20% Gyroid
  - Number of perimeters : 4
  - Number of top/bottom layers : 5
  - Default extrusion width : 0.45mm
  - Perimeters width : 0.45mm
  - External perimeters width : 0.45mm
  - Support : No
  - Brim : No
  - Detect thin walls : No

### Filament type

The parts are designed for PETG and this is what we recommend. Please consider recycled filament and cardboard spool or masterspool. If you are using a different filament material you will need to account for the shrinkage in XY plane directly in the slicer.

| Part | Quantity | Filament | Color | Comment |
|---|:---:|:---:|:-----:|---|
| e_fs_adapter_rev_bowden_no_collet  | 1 | PETG |  Any  | For extruder mount option 1 |
| e_fs_adapter_rev_bowden_e3d_collet | 1 | PETG |  Any  | For extruder mount option 2 |
| e3d_collet_clip | 1 | PETG |  Any  | For extruder mount option 2 |
| frame_mount_standard | 1 | PETG |  Any  | For frame mount option 1 |
| frame_mount_angled | 1 | PETG |  Any  | For frame mount option 2 |

### Assembly

1. Remove the filament from the extruder
2. Unscrew the filament sensor cover and the filament sensor PCB.
3. Remove the e_fs_adapter and the steel ball. Place the ball in the new e_fs_adapter_bowden and insert both in the extruder body (move the filament sensor lever to help with the insertion)
4. If you use the extruder mount option 2, insert the E3D collet into the printed part e_fs_adapter_rev_bowden_e3d_collet
5. Screw back the filament sensor PCB and cover
6. Thread the PC4-M10 fittings in the frame mount of your choice
7. Attach the frame mount to the frame
8. Cut the PTFE at the desired length
9. Insert one side of the PTFE tube inside the extruder mount printed part
10. If you use the extruder mount option 2, lock the PTFE tube with the 3D printed e3d_collet_clip
11. Insert the other side of the PTFE tube inside the PC4-M10

### CAD Files

The native CAD (Fusion) and STEP files are available at [`/cad/optional_parts`](/cad/optional_parts)

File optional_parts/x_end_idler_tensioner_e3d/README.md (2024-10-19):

# BearExxa V2

## X-end idler tensioner for E3D toothed idler

### Introduction

This is a X end idler tensioner compatible with E3D toothed idler.

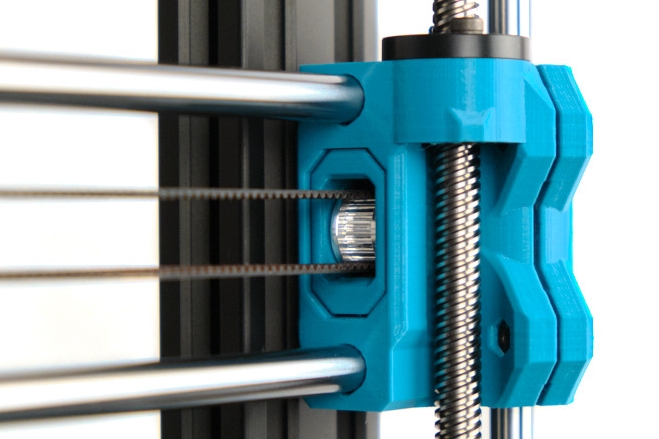
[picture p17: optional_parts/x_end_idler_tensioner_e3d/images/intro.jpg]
Introduction X end E3D idler


### Bill of materials

| Part | Quantity | Comment/Link |
|---|:---:|---|
| Bear X axis | 1 | From version 0.6.0-a and greater |
| E3D Gates 2GT Toothed Idler, 6mm Belt, 20 Tooth, 5mm ID | 1 | [E3D ljnk](https://e3d-online.com/products/gates-belts-pulleys-and-idlers) |
| Dowel pin, dia: 4.95mm (+0.00/-0.05), length: 15.8mm (+0.00/-0.05) | 1 | Must fit the 2GT idler bearing.<br/>:pushpin: Cut a M5 screw if you can't find one |
| M3 Hex nylock nuts (DIN 985) | 2 | Same as original Bear X end idler tensioner |

### Printed parts

Download all optional parts with the button at [Repo Homepage -> Optional Parts -> Official optional parts](/README.md#official-optional-parts)

### Print settings

> [!WARNING]
> The parts have been designed and tested with the parameters below and it is important to follow them to avoid issues like part cracking, bad bridging, not enough stiffness or wrong tolerances. You must [**calibrate your extrusion multiplier**](https://guides.bear-lab.com/Guide/Extrusion+multiplier+and+filament+diameter/8?lang=en) before printing the parts.

You can use the default PrusaSlicer print profile *0.20mm QUALITY @MK3* with 4 perimeters and 5 tops/bottoms layers and 20% infill. Otherwise, here are the parameters we recommend:

  - Slicer : PrusaSlicer
  - Nozzle size : 0.4mm
  - Layer height : 0.2mm
  - Infill : 20% Cubic or 20% Gyroid
  - Number of perimeters : 4
  - Number of top/bottom layers : 5
  - Default extrusion width : 0.45mm
  - Perimeters width : 0.45mm
  - External perimeters width : 0.45mm
  - Support : No
  - Brim : No
  - Detect thin walls : No

### Filament type

The parts are designed for PETG and this is what we recommend. Please consider recycled filament and cardboard spool or masterspool. If you are using a different filament material you will need to account for the shrinkage in XY plane directly in the slicer.

| Part | Quantity | Filament | Color |
|---|:---:|:---:|:-----:|
| x_end_idler_tensioner_e3d  | 1 | PETG |  Any  |

### Credits

Thanks to Matthew Humphrey for having created the first version of this idler.
[thingiverse.com/thing:3308226](https://www.thingiverse.com/thing:3308226)

What has changed from Matthew's design:
  - Improves shape and tolerances around the E3D idler
  - Derivation from the original design (using Fusion derive feature)

### CAD Files

This is the exact same design than the on the BearExxa V1 and the CAD files are available on the [BearExxa V1 GitHub1 repository](https://github.com/gregsaun/bear_extruder_and_x_axis).

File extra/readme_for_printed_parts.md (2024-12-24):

# BearExxa V2

Follow the steps from the "How To" to print, build and start using the BearExxa V2:
https://github.com/gregsaun/BearExxa-V2?tab=readme-ov-file#how-to

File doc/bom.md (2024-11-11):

# BearExxa V2

## Bill of Materials

### Introduction

The hardware list below is to build the extruder and X from scratch. It does include all the hardware like if you didn't have a printer. In the tables below, the column "Reused from Prusa" indicates that you can reuse the part from your Original Prusa MK2.5(S, S+) or MK3(S, S+).

### Hardware X Axis

| Part | Quantity | Comment / Links | Reused from Prusa |
|---|:---:|:---|:---:|
| M2x12 (ISO 4762) | 2 | :warning: MK2.5(S, S+) only | no |
| M3x10 (ISO 4762) | 6 | | no |
| M3x18 (ISO 4762) | 9 | | no |
| M3 hex nut (ISO 4032) | 10 | | no |
| M3 hex nylock nuts (DIN 985) | 2 | | no |
| Dowel pin, dia 2.90mm +/-0.05, length 15.8mm +/-0.1 | 1 | Cut an M3 screw if you can't find one | no |
| 2GT 16T pulley 5mm bore | 1 | | yes |
| 2GT 20T idler 3mm bore | 1 | | yes |
| Bearings LM8UU | 4 | | yes |
| Smooth rods, dia 8mm H6, length 370mm | 2 | | yes |
| Belt Gates LL-2GT RF, width 6mm, length 880mm | 1 | | yes |

### Hardware Extruder

| Part | Quantity | Comment / Link | Reused from Prusa |
|---|:---:|:---|:---:|
| M2x8 (ISO 4762) | 1 | | no |
| M3x6 button head (ISO 7380) | 2 | | no |
| M3x10 (ISO 4762) | 8 | | no |
| M3x18 (ISO 4762) | 8 | | no |
| M3x30 (ISO 4762) | 6 | | no |
| M3x40 (ISO 4762) | 2 | | no |
| M3x50 (ISO 4762) | 2 | | no |
| M3 square nut (DIN 562) | 14 | | no |
| M3 hex nut (ISO 4032) | 8 | | no |
| M3 washer (DIN 125) | 2 | | no |
| PTFE tube 4x2, length 32mm +0.0/-0.5 | 1 | | no |
| Bondtech drivegear 1.75/5.0 (dual hobb gears) | 1 | | yes |
| Bondtech motor gear 17 teeth | 1 | [Bondtech store](https://www.bondtech.se/product/motor-gear) | no |
| Bondtech shaft assembly gear 50 teeth | 1 | [Bondtech store](https://www.bondtech.se/product/shaft-assembly) | no |
| Bondtech shaft 3x20 | 1 | [Bondtech store](https://www.bondtech.se/product/shafts) | yes |
| Bondtech shaft 3x32 | 1 | [Bondtech store](https://www.bondtech.se/product/shafts) | no |
| MR105 ZZ bearing (10x5x4) | 2 | | no |
| E3D Revo Micro heatsink | 1 | [E3D store](https://e3d-online.com/products/revo-micro-heatsink) | no |
| E3D Revo Micro fan | 1 | [E3D store](https://e3d-online.com/products/revo-micro-fan) | no |
| E3D Revo 0.4mm brass nozzle | 1 | [E3D store](https://e3d-online.com/products/revo-nozzles?variant=40923127808059) | no |
| E3D Revo Heater Core 12V/24V 40W 104-NT | 1 | 12V for MK2.5(S, S+)<br>24V for MK3(S, S+)<br>[E3D store](https://e3d-online.com/products/revo-heatercore?variant=39842664874043) | no |
| Pancake motor Nema 17 25mm LDO 42STH25-1004AC or Bondtech BMG OSM 17HS10-0704S | 1 | [Bondtech store](https://www.bondtech.se/product/nema17-pancake-stepper-25mm) | no |
| Prusa filament sensor with cable | 1 | | yes |
| Prusa 7mm steel ball | 1 | | yes |
| Prusa 20x6x2 magnet | 1 | | yes |
| Prusa 10x6x2 magnet | 1 | | yes |
| Prusa Pinda V2 or SuperPinda | 1 | | yes |
| Prusa extruder spring | 1 | | yes |
| Bearings LM8UU | 3 | | yes |
| Nylon cable, dia 2.85-3mm, length 500mm | 1 | | yes |
| Zip ties 2.5x100mm | 4 | | no |

### Printed Parts

| Part | Quantity | Comment |
|---|:---:|:---|
| e_bearing_screw | 1 | |
| e_body | 1 | |
| e_cover | 1 | |
| e_fan_mount | 1 | |
| e_fs_adapter | 1 | |
| e_fs_cover | 1 | |
| e_fs_lever | 1 | |
| e_groove_mount | 1 | |
| e_motor_plate | 1 | |
| e_nozzle_fan_duct | 1 | |
| e_pinda_mount | 1 | |
| e_tensioner | 1 | |
| tool_ptfe_cutter_32mm | 1 | |
| x_carriage | 1 | |
| x_carriage_back | 1 | |
| x_carriage_mk2_cable_guide | 1 | MK2.5, MK2.5S, MK2.5S+ only |
| x_carriage_mk2_endstop | 1 | MK2.5, MK2.5S, MK2.5S+ only |
| x_carriage_mk3_cable_guide | 1 | MK3, MK3S and MK3S+ only |
| x_end_idler | 1 | |
| x_end_idler_tensioner | 1 | |
| x_end_motor_mk2 | 1 | MK2.5, MK2.5S, MK2.5S+ only |
| x_end_motor_mk3 | 1 | MK3, MK3S and MK3S+ only |

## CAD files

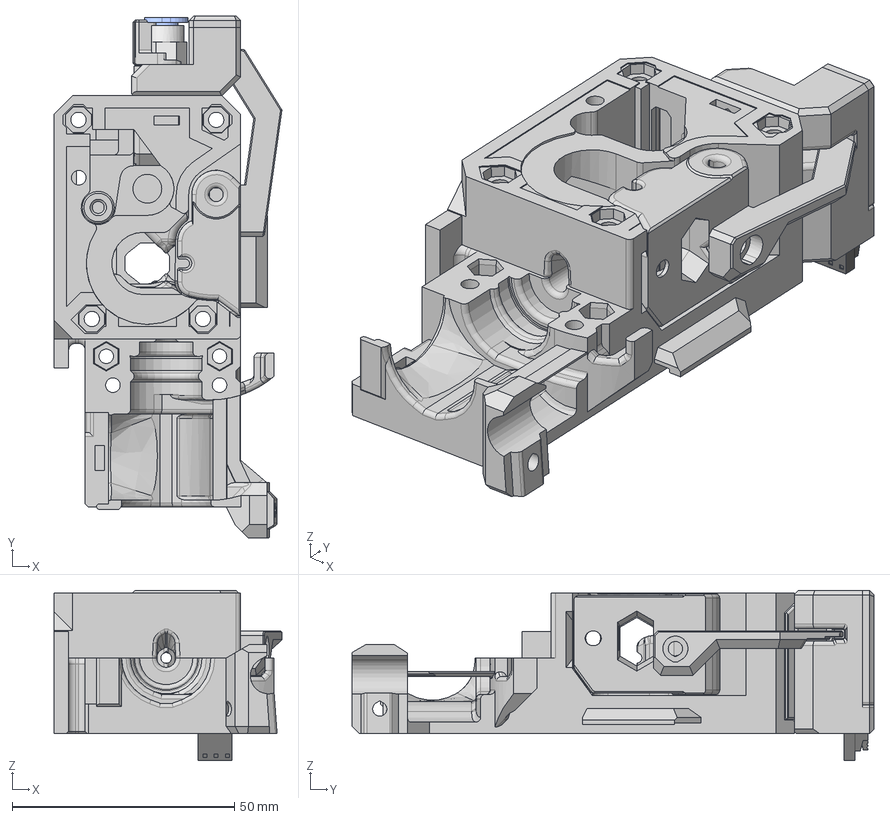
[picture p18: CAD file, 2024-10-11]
cad/optional_parts/mmu/e_body_mmu_assembly.step
51.3 x 117.5 x 38.3 mm
insert_tappex_microbarb_m5
festo_qsm-m5-4
e_fs_cover_mmu2s
e_fs_chimney_mmu2s_1
mkxs_ir_sensor v4
molex_sl_3pin
e_fs_chimney_cover_mmu2s
e_tensioner_mmu2s
e_fs_lever_mmu2s
e3d_collet_175
e_fs_adapter_mmu2s_e3d_clip

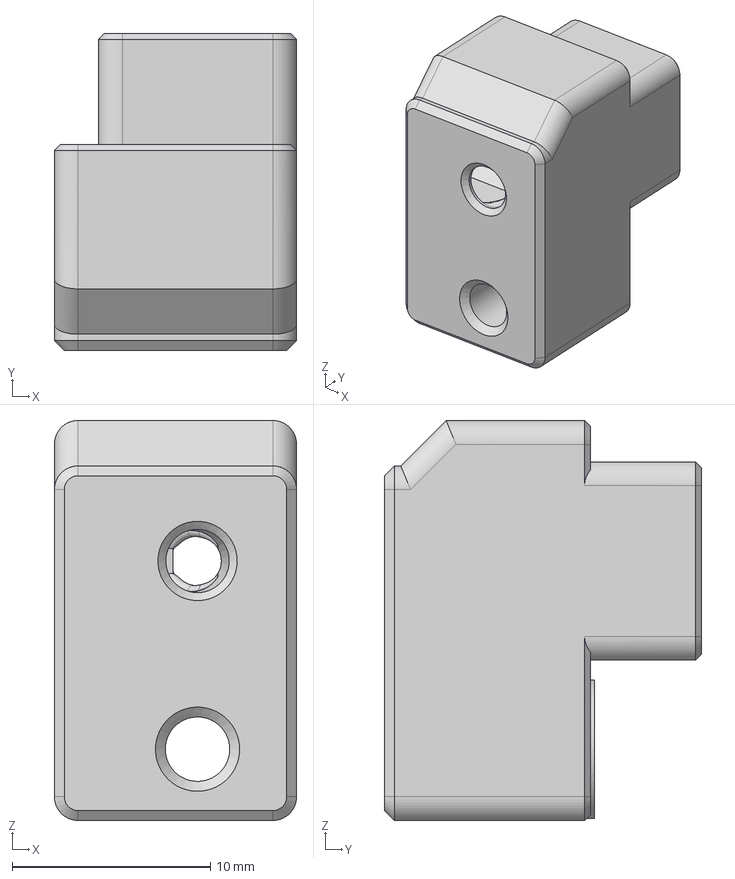
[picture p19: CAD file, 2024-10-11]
cad/optional_parts/reverse_bowden/e_fs_adapter_rev_bowden_e3d_collet.step
12.2 x 16.0 x 20.2 mm

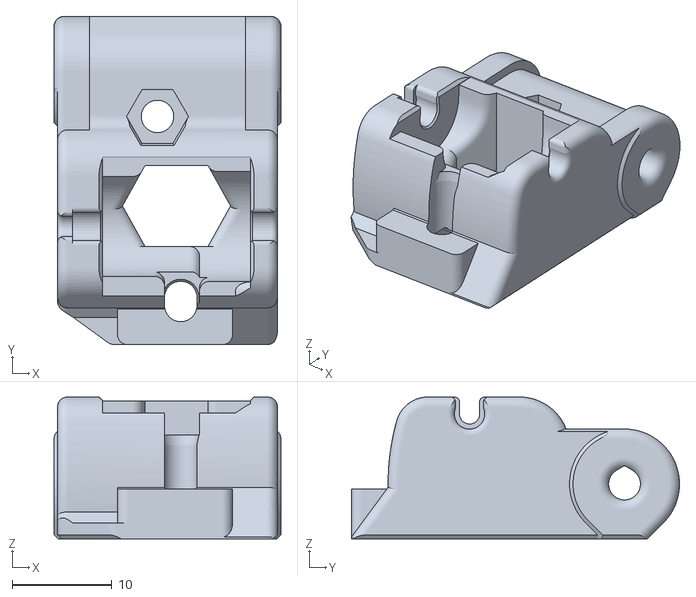
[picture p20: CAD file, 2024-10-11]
optional_parts/mmu_ercf/printed_parts/stl/e_tensioner_mmu2s.stl
22.7 x 32.8 x 14.2

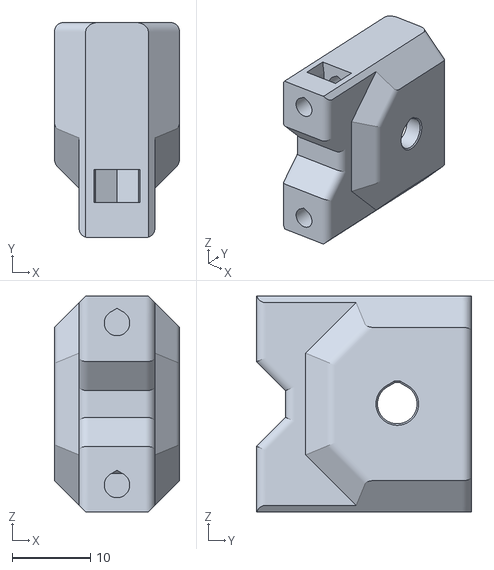
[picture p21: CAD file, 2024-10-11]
optional_parts/x_end_idler_tensioner_e3d/printed_parts/stl/x_end_idler_tensioner_e3d.stl
16.0 x 27.5 x 27.6

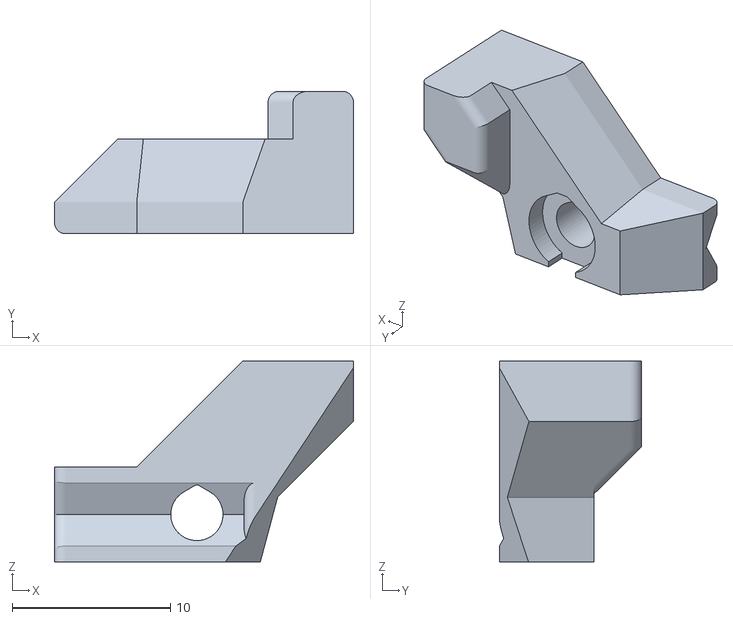
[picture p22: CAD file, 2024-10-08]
printed_parts/stl/x_carriage_mk2_endstop.stl
18.9 x 9.00 x 12.7

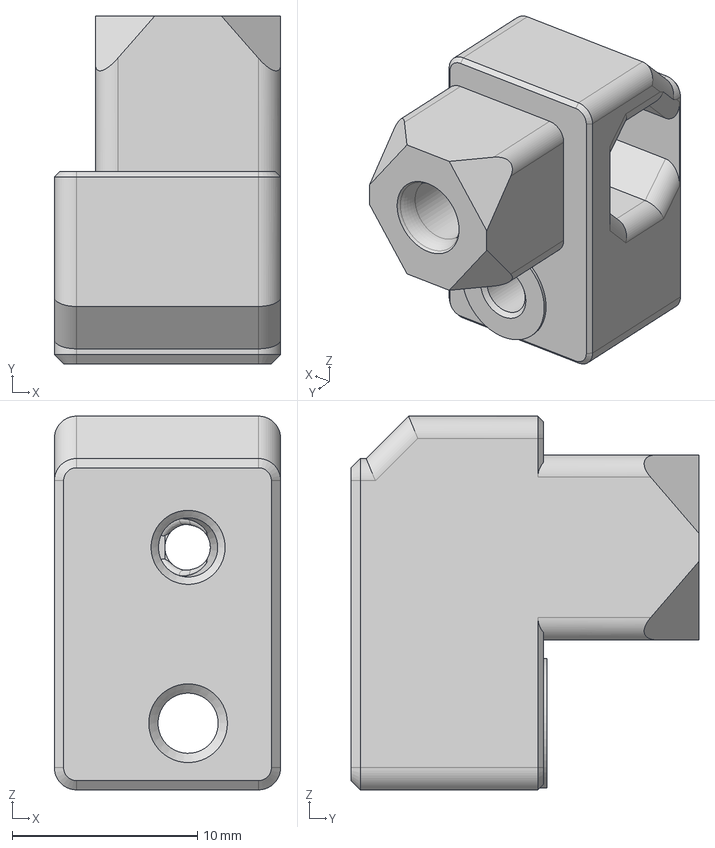
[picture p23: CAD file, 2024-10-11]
cad/optional_parts/reverse_bowden/e_fs_adapter_rev_bowden_no_collet.step
12.2 x 18.8 x 20.2 mm

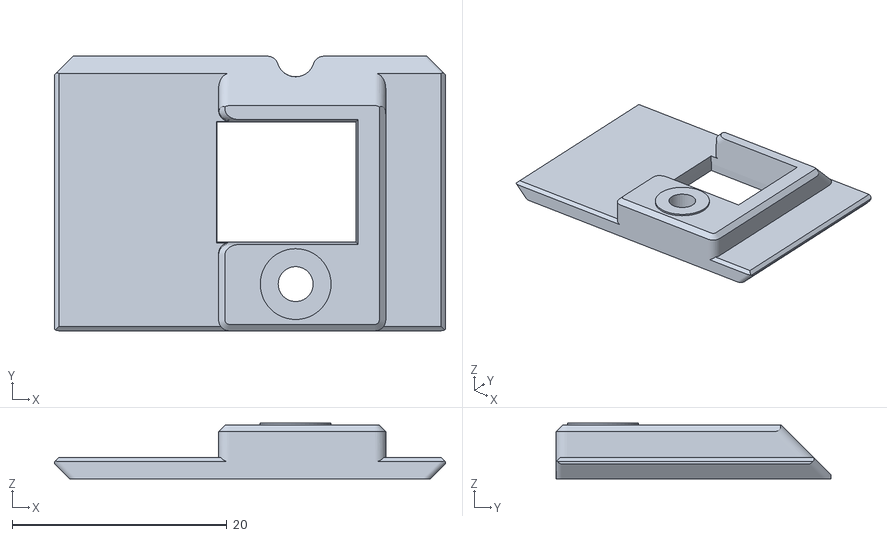
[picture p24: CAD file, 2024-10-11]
optional_parts/mmu_ercf/printed_parts/stl/e_fs_cover_mmu2s.stl
36.4 x 25.6 x 5.20

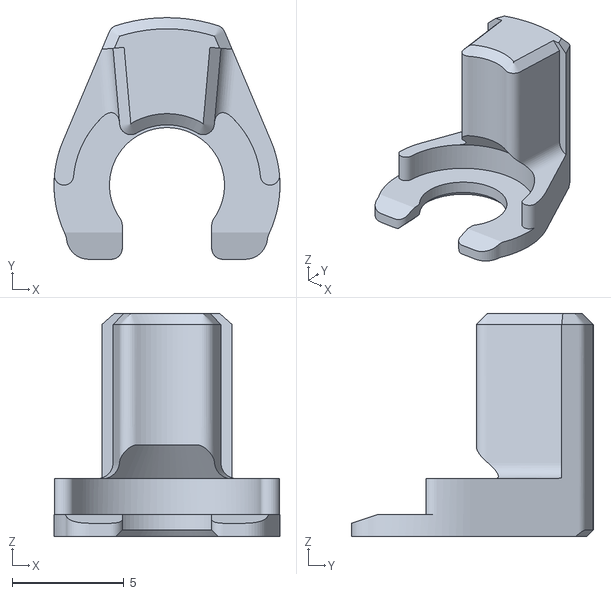
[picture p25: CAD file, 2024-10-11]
optional_parts/reverse_bowden/printed_parts/stl/e3d_collet_clip.stl
10.1 x 10.8 x 10.0

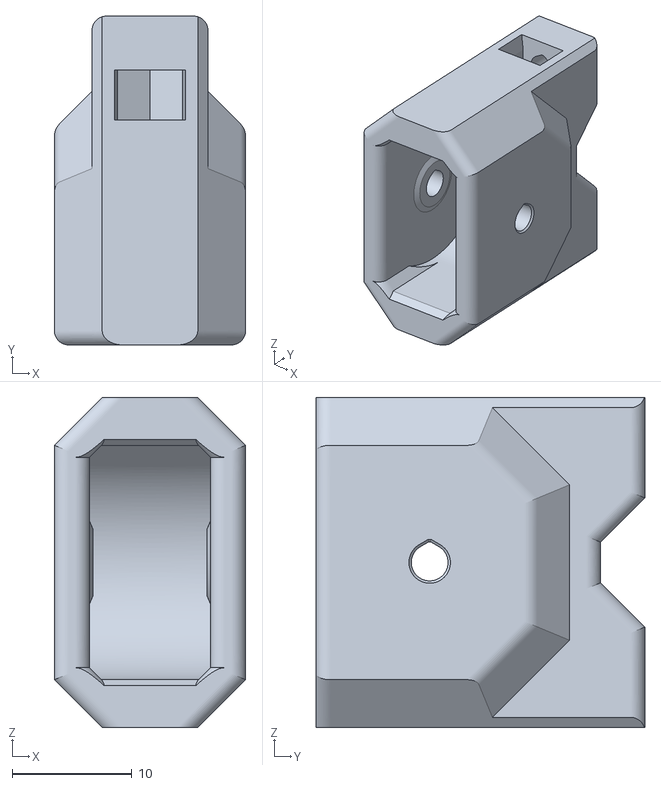
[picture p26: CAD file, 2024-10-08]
printed_parts/stl/x_end_idler_tensioner.stl
16.0 x 27.5 x 27.6

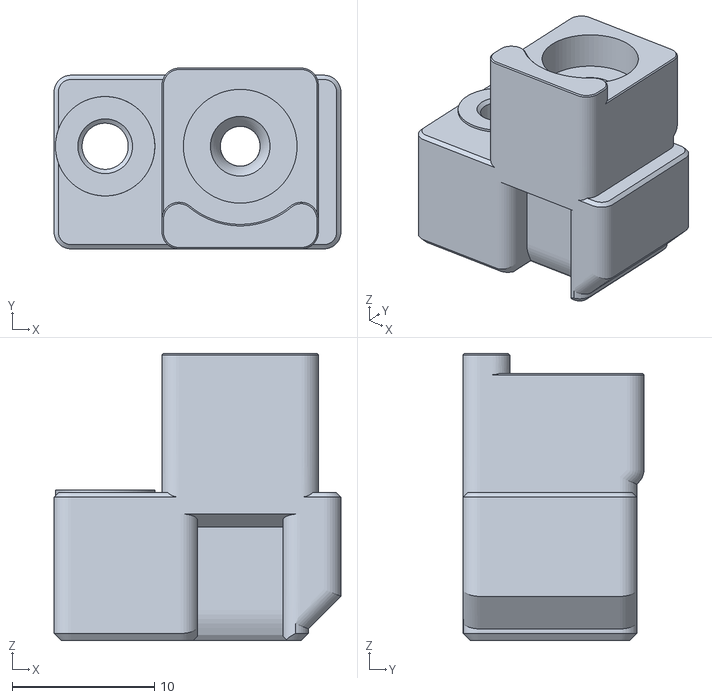
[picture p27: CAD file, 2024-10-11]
optional_parts/mmu_ercf/printed_parts/stl/e_fs_adapter_mmu2s_prusa.stl
20.2 x 12.7 x 20.2

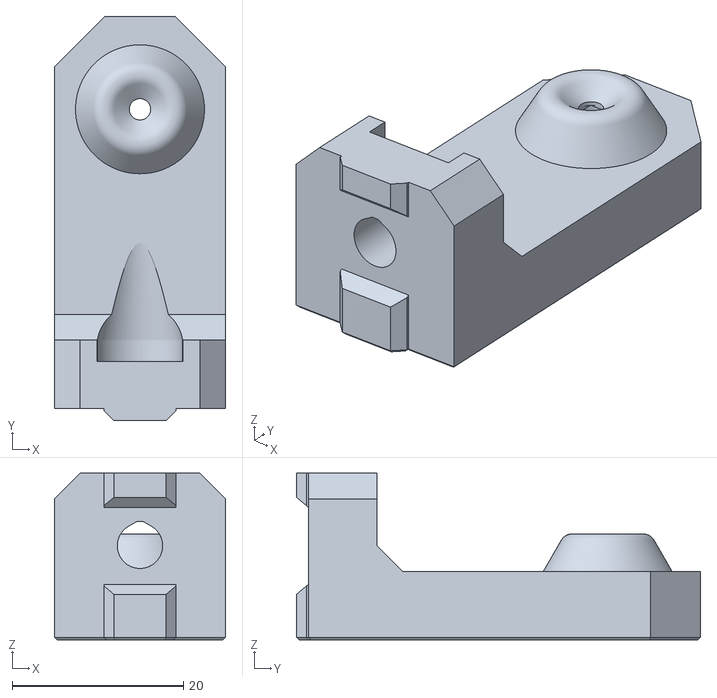
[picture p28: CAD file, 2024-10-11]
optional_parts/reverse_bowden/printed_parts/stl/frame_mount_standard.stl
20.0 x 47.3 x 19.5

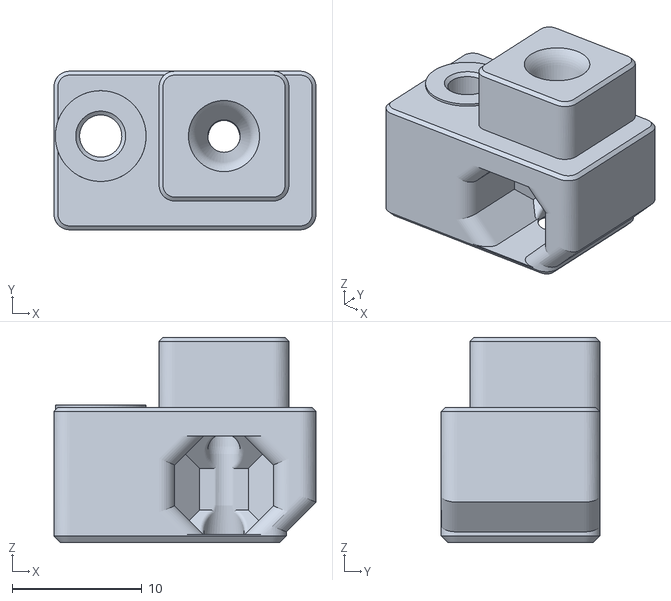
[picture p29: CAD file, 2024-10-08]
printed_parts/stl/e_fs_adapter.stl
20.2 x 12.2 x 15.8

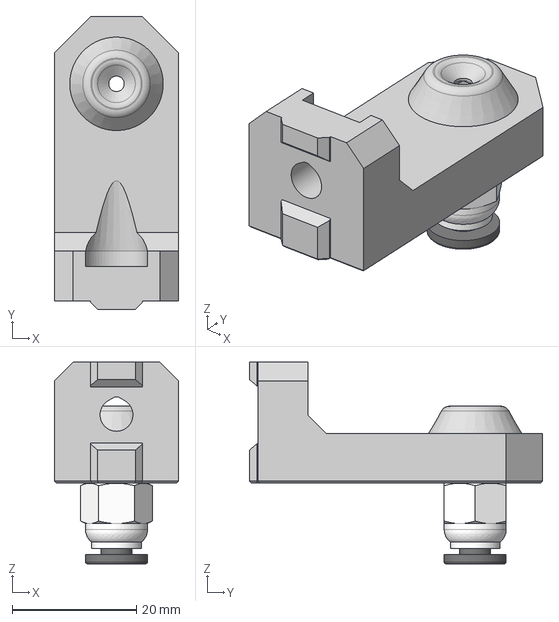
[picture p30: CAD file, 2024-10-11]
cad/optional_parts/reverse_bowden/frame_mount_standard.step
20.0 x 47.3 x 32.5 mm

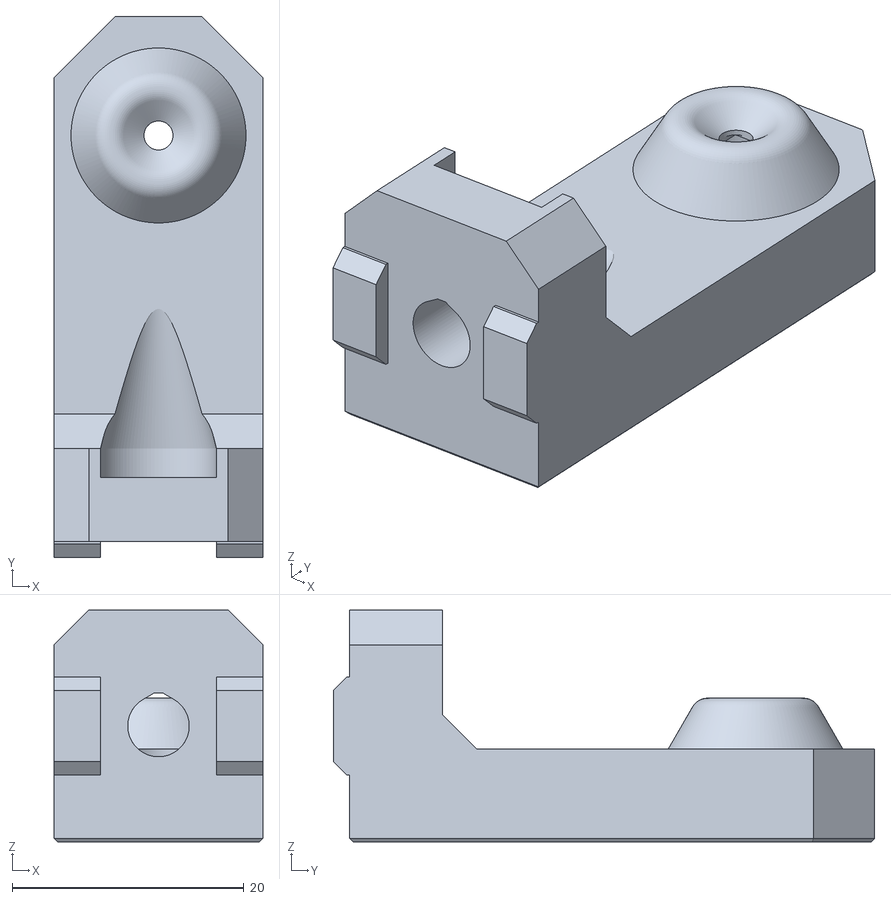
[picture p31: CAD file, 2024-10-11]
optional_parts/reverse_bowden/printed_parts/stl/frame_mount_angled.stl
18.0 x 46.7 x 20.0

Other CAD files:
optional_parts/reverse_bowden/printed_parts/stl/e_fs_adapter_rev_bowden_e3d_collet.stl
cad/optional_parts/reverse_bowden/e3d_collet_clip.step
printed_parts/stl/e_groove_mount.stl
cad/optional_parts/reverse_bowden/e3d_collet_clip.f3d
cad/optional_parts/reverse_bowden/frame_mount_angled.f3z
cad/optional_parts/reverse_bowden/frame_mount_angled.step
cad/optional_parts/reverse_bowden/frame_mount_standard.f3z
optional_parts/mmu_ercf/printed_parts/stl/e_fs_adapter_mmu2s_e3d.stl
optional_parts/mmu_ercf/printed_parts/stl/e_fs_chimney_cover_mmu2s.stl
optional_parts/mmu_ercf/printed_parts/stl/e_fs_chimney_mmu2s.stl
optional_parts/mmu_ercf/printed_parts/stl/e_fs_lever_mmu2s.stl
optional_parts/reverse_bowden/printed_parts/stl/e_fs_adapter_rev_bowden_no_collet.stl
printed_parts/stl/e_bearing_screw.stl
printed_parts/stl/e_body.stl
printed_parts/stl/e_cover.stl
printed_parts/stl/e_fan_mount.stl
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

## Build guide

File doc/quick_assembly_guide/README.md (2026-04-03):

# BearExxa V2

## Quick Assembly Guide

This guide is only for the beta version. It's provided at your own risk.

> [!TIP]
> Images are clickable for larger view.

### Part 1
  1. Read the [Project Status](/README.md#project-status), [Disclaimer](/README.md#disclaimer) and [Compatibility](/README.md#compatibility) to make sure you agree to the limitations
  2. Get the filament according to the [Print Settings](/README.md#print-settings)
  3. [Download](/README.md#download) the BearExxa V2 files
  4. Calibrate your filaments with our [Calibration Guide](https://guides.bear-lab.com/Guide/Extrusion+multiplier+and+filament+diameter/8)
  5. Slice and print the parts according to the [Print Settings](/README.md#print-settings)

### Part 2
Start by doing the preflight check and disassembly :
  1. With a web browser, go to [https://guides.bear-lab.com -> Extruder and X Axis -> Bear Extruder -> Assembly guide -> 1. Preflight check and disassembly](https://guides.bear-lab.com/Guide/1.+Preflight+check+and+disassembly/34?lang=en)
  2. Follow steps 1 and 2
  3. At step 3, use the printed file *tool_ptfe_cutter_32mm* that comes with BearExxa V2 to cut the PTFE. You only need to make an internal chamfer. The end of the tube that goes in the hotend needs to be cut straight (no external chamfer)
  4. Follow steps 4 to 9

### Part 3
Then Assemble the X Axis :
  1. With a web browser, go to [https://guides.bear-lab.com -> Extruder and X Axis -> Bear Extruder -> Assembly guide -> 2. X Axis](https://guides.bear-lab.com/Guide/2.+X+axis/39?lang=en)
  1. Follow all steps from 1 to 15

### Part 4
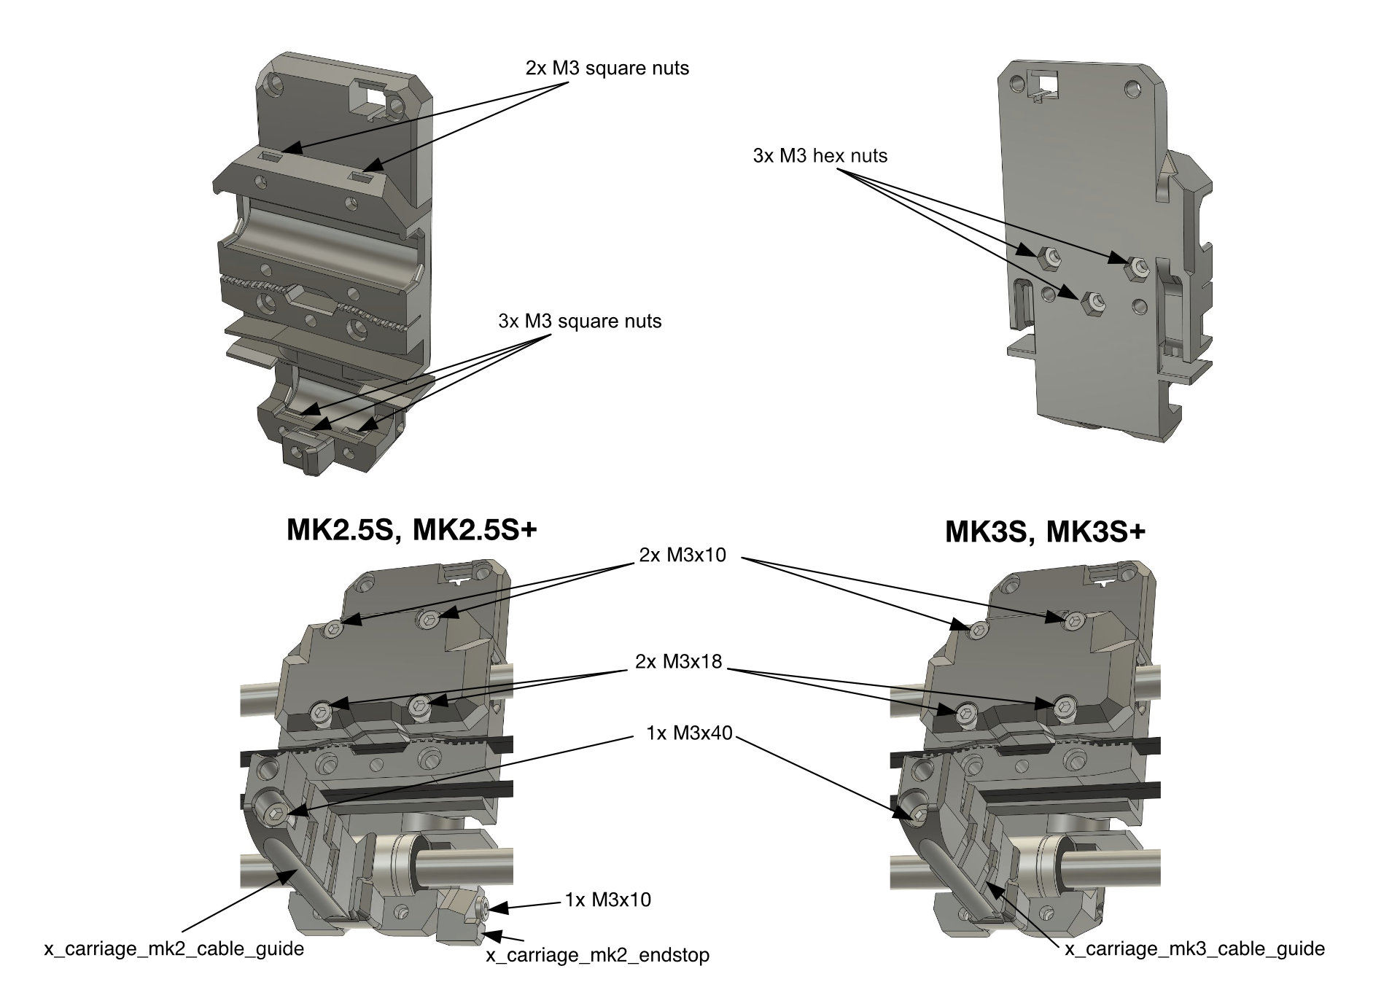
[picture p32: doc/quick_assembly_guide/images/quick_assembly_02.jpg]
Part 2


### Part 5
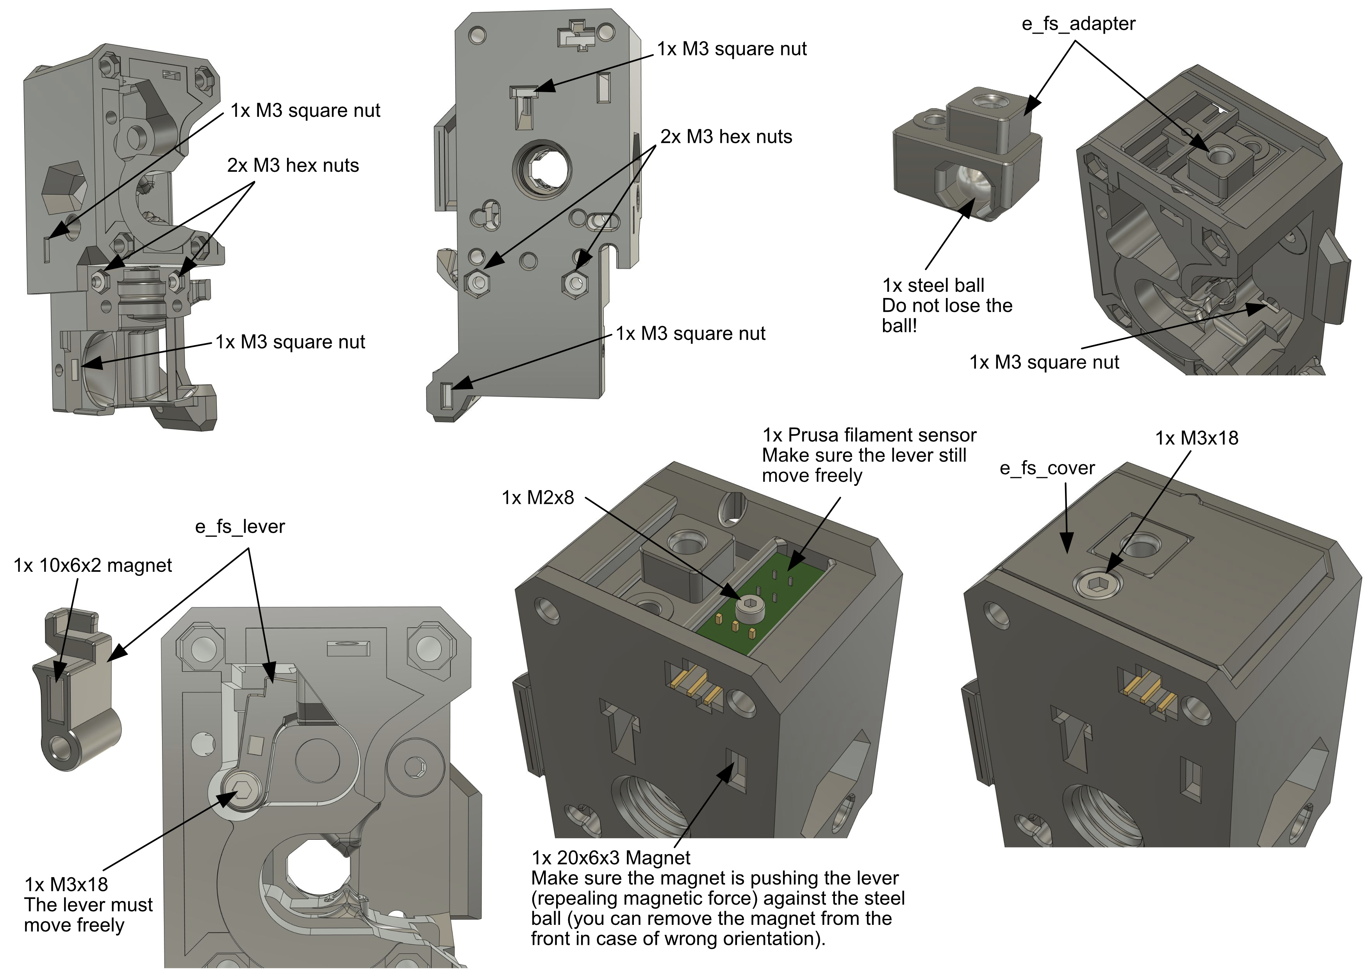
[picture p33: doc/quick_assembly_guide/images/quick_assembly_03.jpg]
Part 3


### Part 6
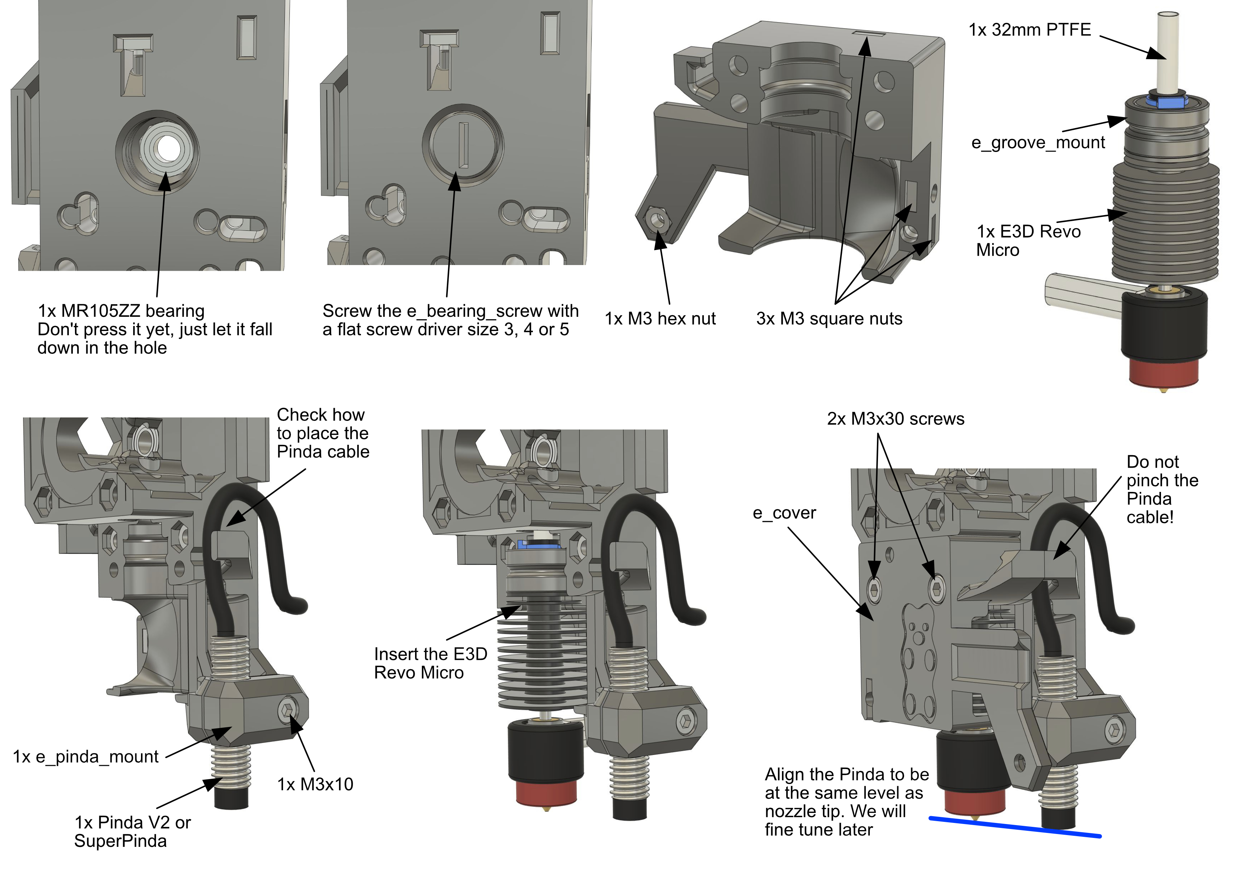
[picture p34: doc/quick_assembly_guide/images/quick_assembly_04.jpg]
Part 4


### Part 7
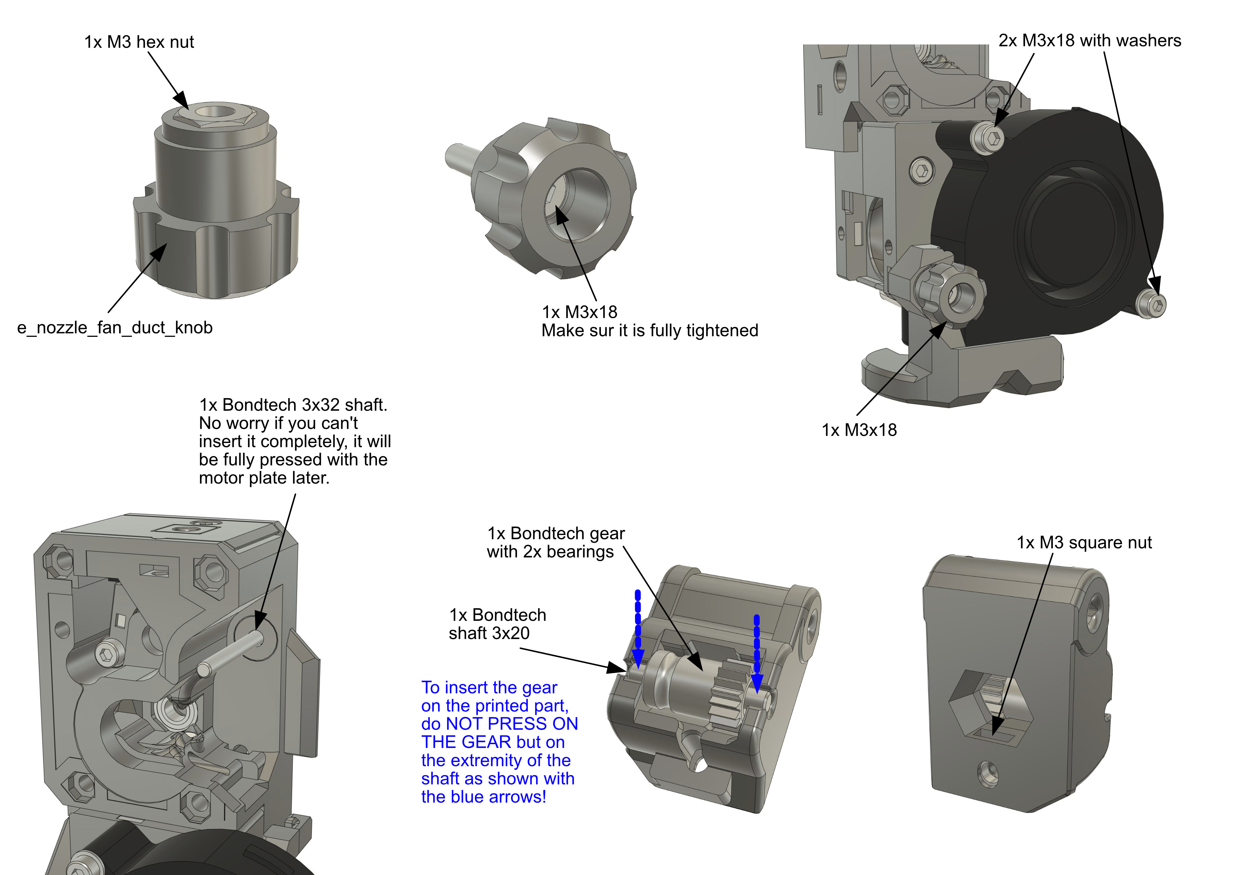
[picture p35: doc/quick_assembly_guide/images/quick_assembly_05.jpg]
Part 5


### Part 8
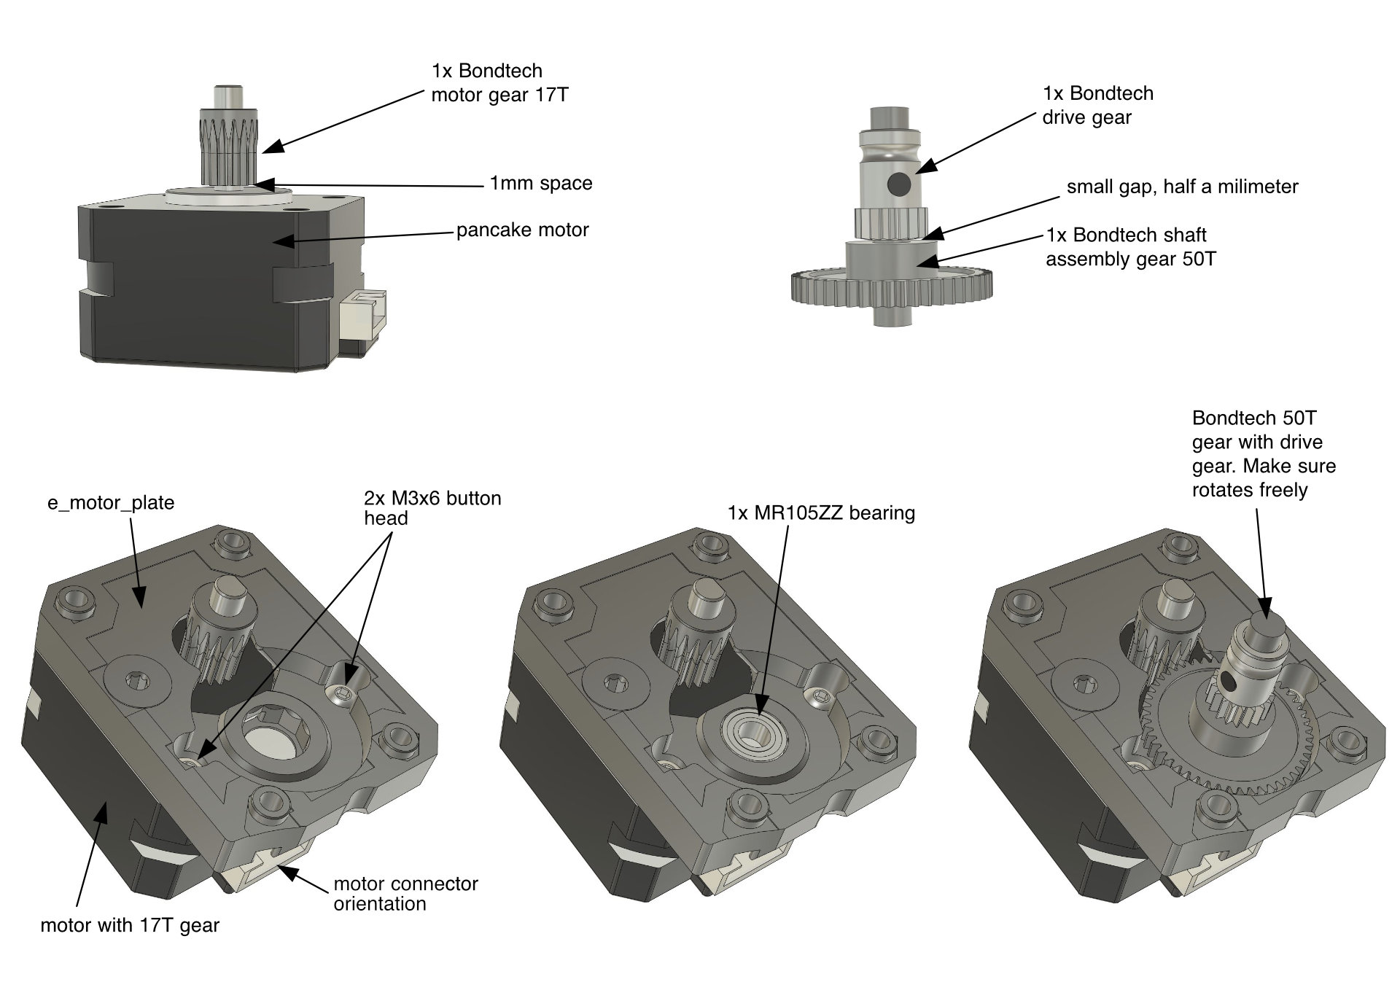
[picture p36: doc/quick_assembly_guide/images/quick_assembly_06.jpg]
Part 6


### Part 9
The connectors should be wired as shown in the image. You may have to swap some wires on the connectors to match the image.

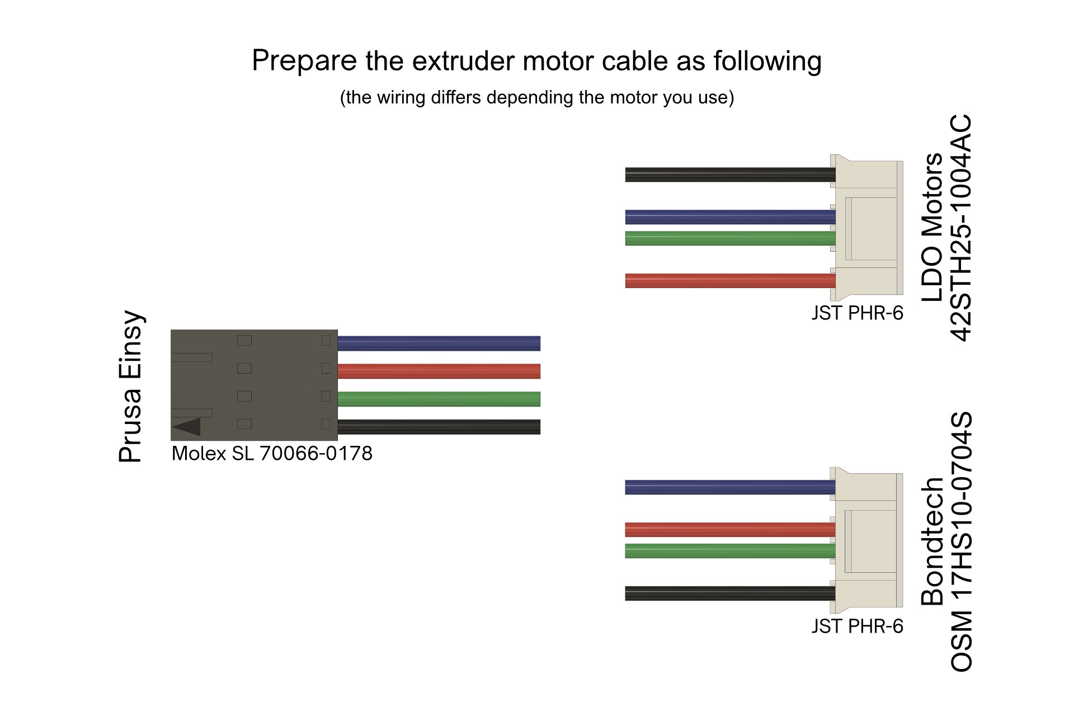
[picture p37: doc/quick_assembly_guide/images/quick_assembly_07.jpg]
Part 7


### Part 10
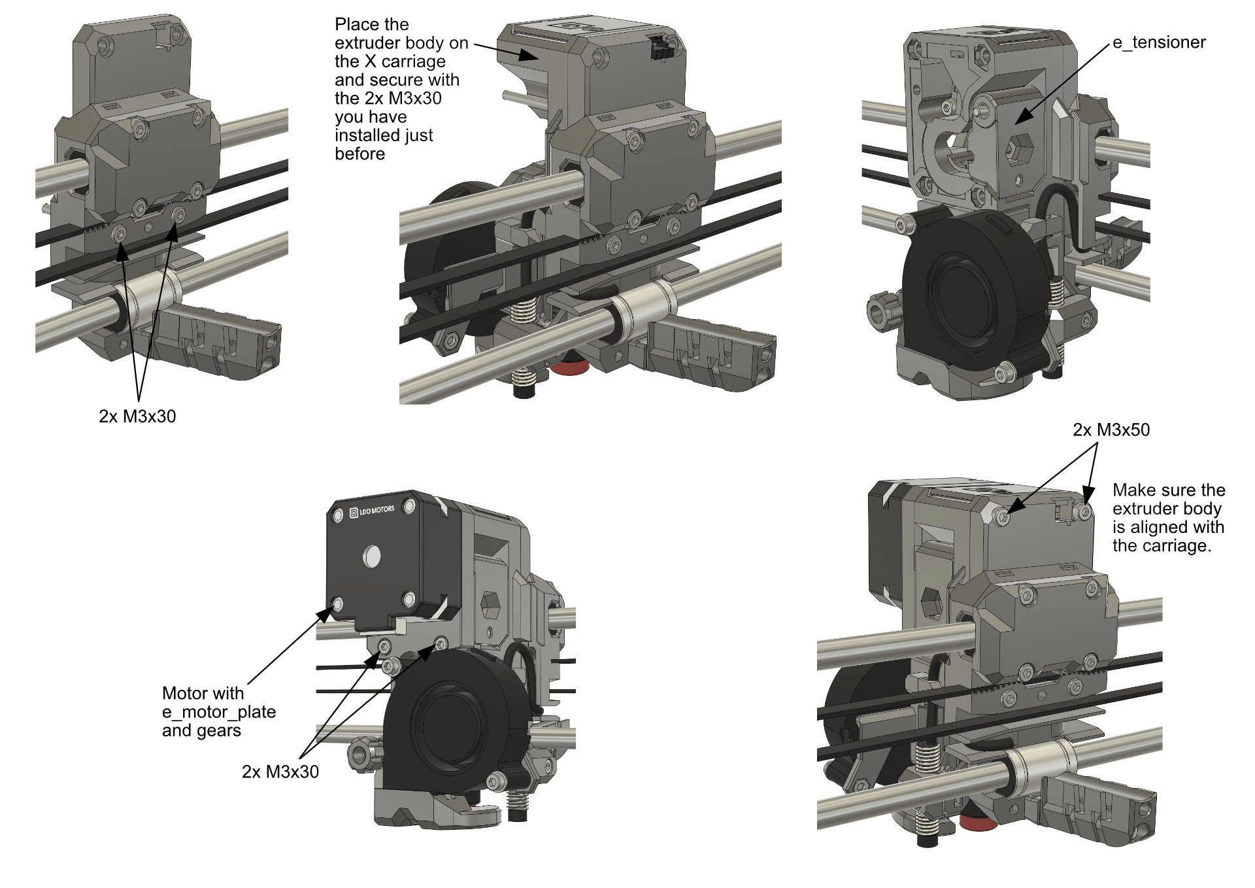
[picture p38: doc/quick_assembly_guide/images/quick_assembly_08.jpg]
Part 8


### Part 11
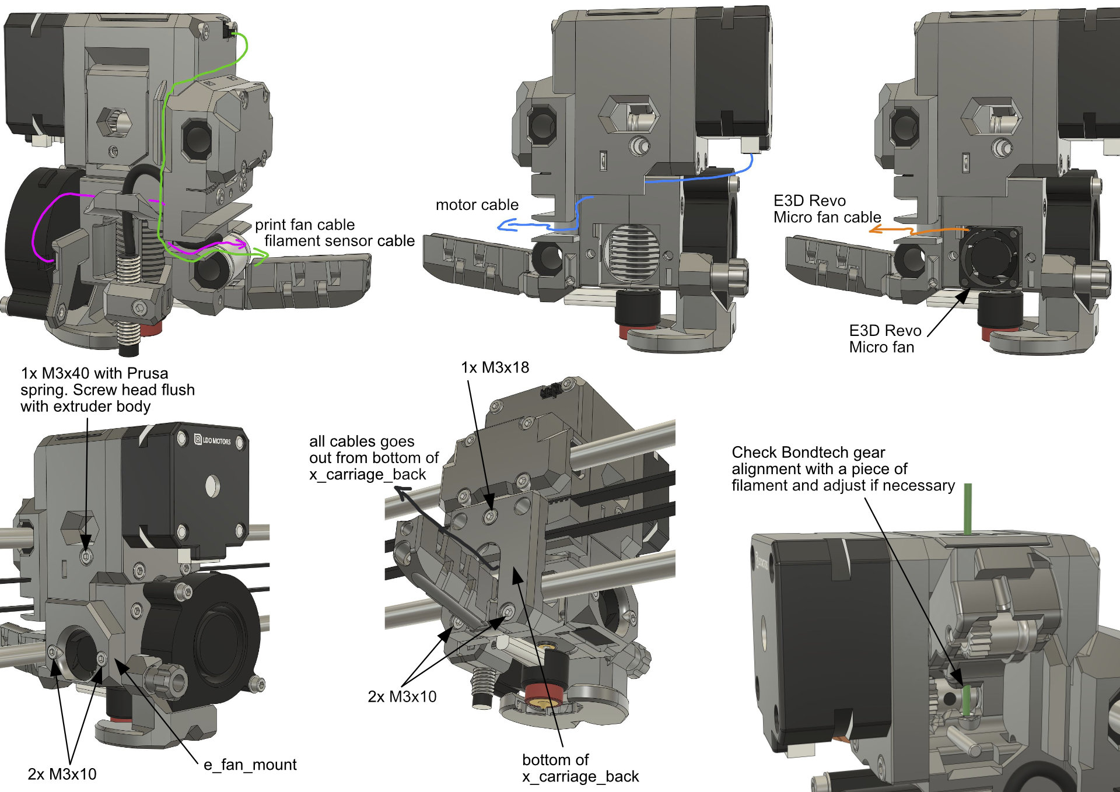
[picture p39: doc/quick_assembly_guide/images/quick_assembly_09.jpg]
Part 9


### Part 12
Route and connect all wires as explained in the Prusa assembly guide.
  - [MK2.5S guide](https://help.prusa3d.com/guide/4-electronics-assembly_62856)
  - [MK3S guide](https://help.prusa3d.com/guide/8-electronics-assembly_34416)
  - [MK3S+ guide](https://help.prusa3d.com/guide/8-electronics-assembly_174100)

For MK3(S, S+), connect the E3D hotend fan cable like this (left: ground, middle: positive, right: not connected):
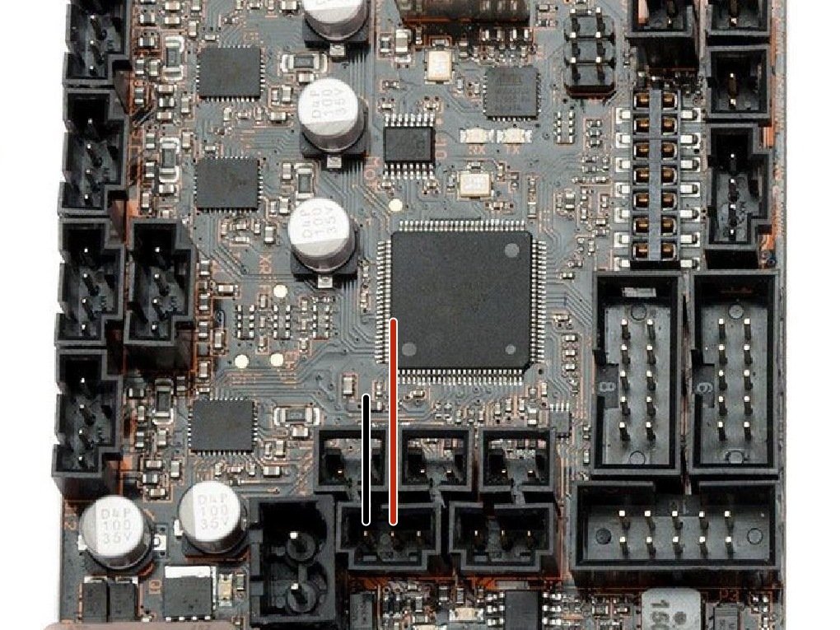
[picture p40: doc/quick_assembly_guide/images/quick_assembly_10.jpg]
Hotend fan wiring MK3


### Part 13
Follow our guide "Final adjustments and calibration" to set the (Super)Pinda height, adjust the belt tension and flash the Bear calibration firmware:
  1. With a web browser, go to [https://guides.bear-lab.com -> Extruder and X Axis -> Bear Extruder> Assembly guide -> 5. Final adjustments and calibration](https://guides.bear-lab.com/Guide/5.+Final+adjustments+and+calibration/38?lang=en)
  1. Follow steps 1 to 12

### Part 14
We now need to configure extruder steps per millimeters to 415 and microstepping to 1/16. You can do this with the provided gcode file :
  1. In the downloaded BearExxa v2 files, go to [config/firmware/prusa_original/config_prusa/](/doc/config/firmware/prusa_original/) 
  1. Copy `bearexxa2_config.gcode` to an SD card
  1. Insert the SD card in your printer and print to `bearexxa2_config.gcode` file
  1. You can now remove the SD card and delete the file

### Part 15
The current E3D Micro hotend fan does not have a tachometer wire so we need to deactivate the fan check:
  1. In the LCD menu, go to `Settings -> Fans Check`
  1. Select `OFF`

> [!TIP]
> The official kit will contains a fan with the tachometer wire and you will not needed to disable this features anymore. 

### Part 16
  1. Temporarily plug the original Prusa hotend fan 40x40 (Noctua or Delta):  
    - [MK3(S, S+) guide](https://help.prusa3d.com/guide/8-electronics-assembly_174100#175539)
    - [MK2.5(S, S+) guide](https://help.prusa3d.com/guide/4-electronics-assembly_62856#62944)
  3. Run the self tests using `LCD Menu -> Calibration -> Selftest`
  4. Once the fan detection is done, plug back the E3D Revo Micro fan
  5. Follow steps 14 to 16

> [!WARNING]
> Any issues reported during the self test must be fixed before continuing further.

### Part 17 (Optional)
This step is optional. It explains how to use the latest Prusa firmware but it's not a necessity nor safer. You can use the Bear calibration firmware to print as a normal Prusa firmware.

First we need to flash the latest Prusa firmware:
  1. Download the [latest Prusa firmware](https://github.com/prusa3d/Prusa-Firmware/releases/latest). You do not need to download the special E3D Revo firmware version 
  2. With a web browser, go to [https://guides.bear-lab.com -> Extruder and X Axis -> Bear Extruder> Assembly guide -> 5. Final adjustments and calibration](https://guides.bear-lab.com/Guide/5.+Final+adjustments+and+calibration/38?lang=en)
  3. Follow step 10 to 12  to flash the latest Prusa firmware (instead of Bear calibration firmware)
  
Then we need to set the hotend fan to always run at 100% speed and disable fan check:
  1. In the LCD menu go to `Settings -> HW Setup`, then scroll to any menu item and hold the knob for 3 seconds until you hear a "click"
  2. Scroll again the same menu and you should now see a new `Experimental` option in the bottom
  3. Enter in this `Experimental` menu and then set `ALTFAN det.` to `OFF`
  4. Go back to the main LCD menu and `Settings -> Fans Check` and select `OFF`
  
Finally we need to disable the new "Thermal Model" for the hotend to rollback to standard PID method used up to Prusa firmware 3.11.x:
  1. Using [Octoprint](https://help.prusa3d.com/article/crash-dump_364959#octoprint) or [PuTTy](https://help.prusa3d.com/article/crash-dump_364959#putty), send the following commands:  
  `M310 S0`  
  `M500`  
  2. In `LCD Menu -> Settings -> Temperature -> Fan speed` set the value at 130 if you print lots of PETG and 255 if you print lots of PLA. For other materials select a value suitable for your most used filament
  3. Run the hotend PID calibration with the `LCD Menu -> Calibration -> PID calibration` for a temperature that matches your most used printing temperature
  4. Once finished, shutdown the printer

> [!TIP]
> You can find more information on the Prusa website about the [experimental menu here](https://help.prusa3d.com/article/experimental-menu-mk3-s-_161213) and the new  ["Thermal Model" here](https://help.prusa3d.com/article/thermal-model-calibration_382488).

### Part 18

We will now configure PrusaSlicer.

We need to reverse the slicing movements to avoid unscrewing the Revo nozzle and reduce the default retraction length as this extruder is more efficient:
  1. In `Printers -> General -> Advanced` check "Prefer clockwise movements"
  2. In `Printers -> Extruder 1 -> Retraction` set "Retraction length" to 0.4mm (good value for PLA, PETG is more around 0.5-0.6mm)
  3. Save your printer profile
  
You will then have to recalibrate your filament profiles for the two following values:
  1. Retune the extrusion multiplier
  2. Retune the Pressure Advance (PA), it may be a little lower compared to stock extruder or BearExxa V1 but it also depends on your print speed. You can change the K value in `Filaments -> Custom G-code -> Start G-code`

> [!TIP]
> If you like to customise your printer's start G-code have a look to the example provided at [/extra/ps_startgcode_bear_mk3s_bex2.gcode](/extra/ps_startgcode_bear_mk3s_bex2.gcode)

### Part 19
All done, enjoy the new extruder and X axis :)

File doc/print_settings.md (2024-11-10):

# BearExxa V2

## Print Settings

### Slicer settings

> [!WARNING]
> The parts have been designed and tested with the parameters below and it is important to follow them to avoid issues like part cracking, bad bridging, not enough stiffness or wrong tolerances. Be sure to have a well calibrated machine and extruder. Check our guide here for [calibrating extrusion multiplier](https://guides.bear-lab.com/Guide/Extrusion+multiplier+and+filament+diameter/8?lang=en)

You can use the default PrusaSlicer print profile *0.20mm QUALITY @MK3* with 4 perimeters and 5 tops/bottoms layers and 20% infill. Otherwise, here are the parameters we recommend:

  * Slicer : PrusaSlicer
  * Nozzle size : 0.4mm
  * Layer height : 0.2mm
  * Infill : 20% Cubic or 20% Gyroid
  * Number of perimeters : 4
  * Number of top/bottom layers : 5
  * Default extrusion width : 0.45mm
  * Perimeters width : 0.45mm
  * External perimeters width : 0.45mm
  * Single perimeter on top layer : No
  * Support : No
  * Brim : No
  * Detect thin walls : No

### Filament type

The parts are designed for PETG and this is what we recommend. Please consider recycled filament and cardboard spool or masterspool. If you are using a different filament material you will need to account for the shrinkage in XY plane directly in the slicer.

| Part | Quantity | Filament | Color | Comment |
|---|:---:|:---:|:-----:|---|
| e_bearing_screw | 1 | PETG |  Any  | |
| e_body | 1 | PETG |  Any  | :warning: do not use single perimeter on top layer |
| e_cover | 1 | PETG |  Any  | |
| e_fan_mount | 1 | PETG |  Any  | |
| e_fs_adapter | 1 | PETG |  Any  | |
| e_fs_cover | 1 | PETG | Black | Read Note 1 |
| e_fs_lever | 1 | PETG | Black | Read Note 1 |
| e_groove_mount | 1 | PETG |  Any  | |
| e_motor_plate | 1 | PETG |  Any  | :warning: do not use single perimeter on top layer | 
| e_nozzle_fan_duct | 1 | Heat Resistant |  Any  | Read Note 2 |
| e_pinda_mount | 1 | PETG |  Any  | |
| e_tensioner | 1 | PETG |  Any  | |
| tool_ptfe_cutter_32mm | 1 | PETG |  Any  | |
| x_carriage | 1 | PETG |  Any  | |
| x_carriage_back | 1 | PETG |  Any  | |
| x_carriage_mk2_cable_guide | 1 | PETG |  Any  | MK2.5, MK2.5S, MK2.5S+ only |
| x_carriage_mk2_endstop | 1 | PETG |  Any  | MK2.5, MK2.5S, MK2.5S+ only |
| x_carriage_mk3_cable_guide | 1 | PETG |  Any  | MK3, MK3S, MK3S+ only |
| x_end_idler | 1 | PETG |  Any  | |
| x_end_idler_tensioner | 1 | PETG |  Any  | |
| x_end_motor_mk2 | 1 | PETG |  Any  | MK2.5, MK2.5S, MK2.5S+ only |
| x_end_motor_mk3 | 1 | PETG |  Any  | MK3, MK3S, MK3S+ only |

Note 1: Avoid eSUN PETG as some user reported that it might not block IR signal correctly. No other PETG have been reported to have this issue yet.

Note 2: If you are only printing PLA and o ly occasionally PETG with your 3D printer then the e_nozzle_fan_duct can be made out of PETG. If you are printing warmer material we recommend to use a heat resistant filament like ABS, ASA, PC, Extrudr GreenTec or Fillamentum NonOilen®. **Don't forget to compensate for shrinkage** accordingly to the filament type you are using.

> [!CAUTION]
> When using ABS, ASA, Nylon or PC filaments you must have a certified filtered enclosure. We recommend to look at brands like [Bofa](https://bofainternational.com) (available at PrintedSolid) or [Alveo3D](https://www.alveo3d.com).

> [!CAUTION]
> We highly recommend to avoid high flow filaments (worse material properties as non high flow) as well as glass fiber or carbon fibers filled filament (whatever if it's PAN-based or pitch-based) as it could be carcinogenic. For more information, please read [this article by Maya Posch from Hackaday](https://hackaday.com/2024/08/07/on-carbon-fiber-types-and-their-carcinogenic-risks/). It will not improve the print quality and could actually make the parts more brittle.

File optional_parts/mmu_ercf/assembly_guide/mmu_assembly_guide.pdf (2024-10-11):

## BearExxa V2 MMU2S Assembly Guide

1. Disconnect the extruder motor cable as we will remove it temporarily. Then unscrew the M3x40 (with spring) of the tensioner and the two M3x30 of the

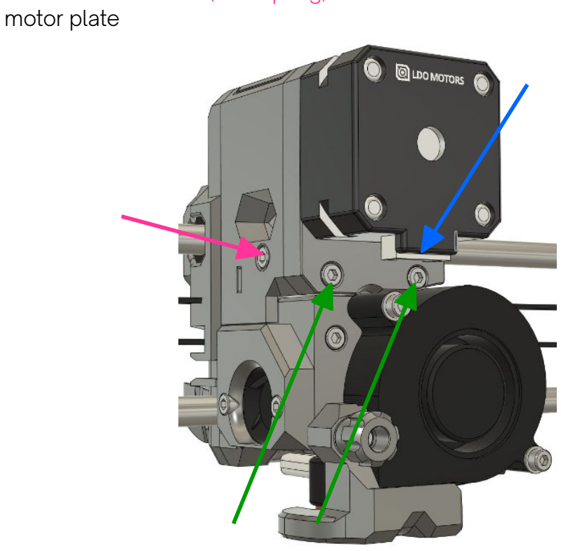
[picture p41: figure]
motor plate

2. Release the two M3x50 screw and remove the motor with the plate and gears

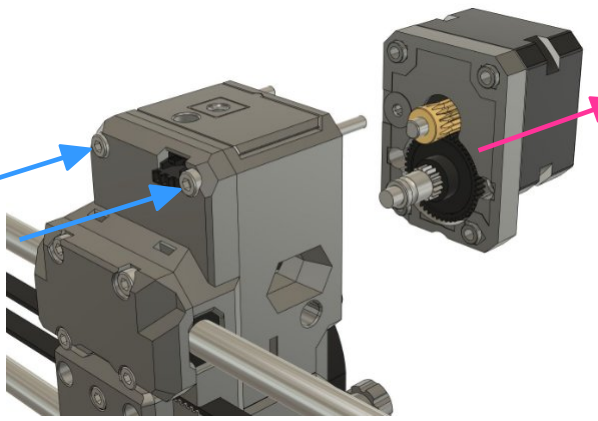
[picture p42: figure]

3. Remove the standard e_tensioner

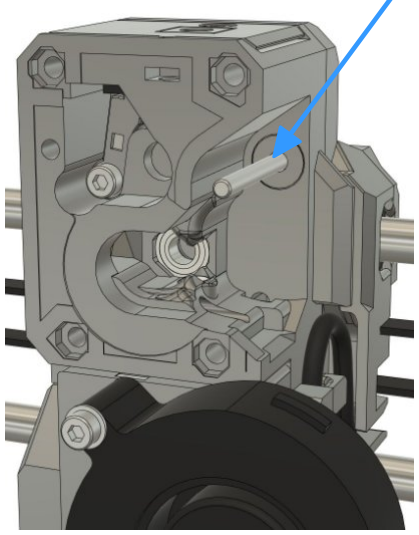
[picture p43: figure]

4. Swap the shaft with bearings and Bondtech gears from the standard e_tensioner to the e_tensioner_mmu2s (do not press on the Bondtech gear to insert it but on both side of the shaft). Insert one M3 hex nut. Then insert the M3 square nut from the other side

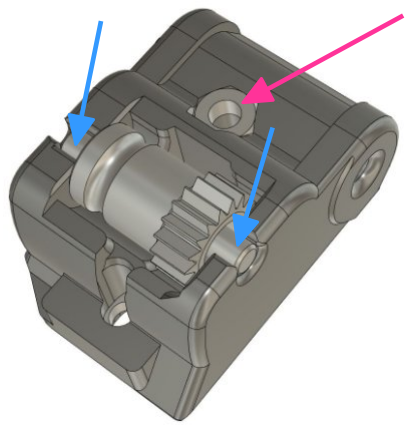
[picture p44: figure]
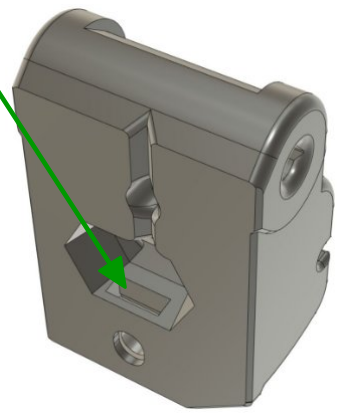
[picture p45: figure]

5. Install the new e_tensioner_mmu2s on the extruder body and screw back the motor and the tensioner screw (see step 1 and 2)

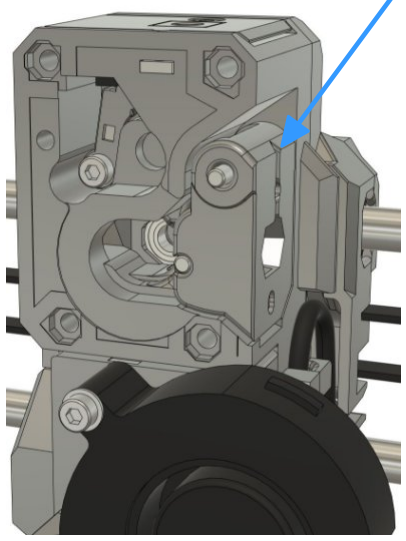
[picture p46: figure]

6. Unscrew the M3x18 and remove the e_fs_cover

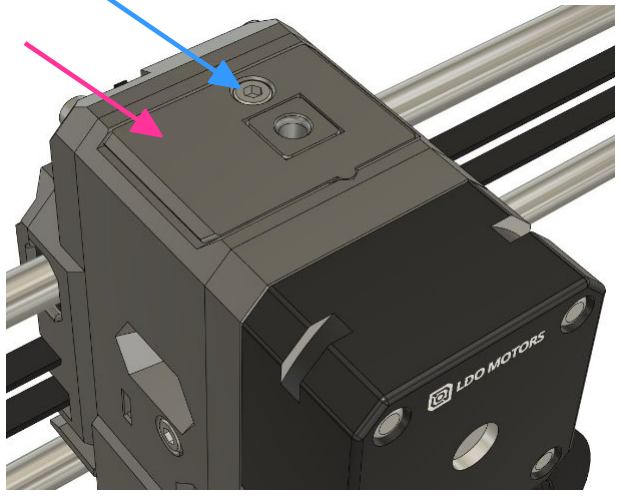
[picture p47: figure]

7. Unscrew the M2x12 and remove the filament sensor. Remove the e_fs_adapter as well (be careful with the metal ball inside).

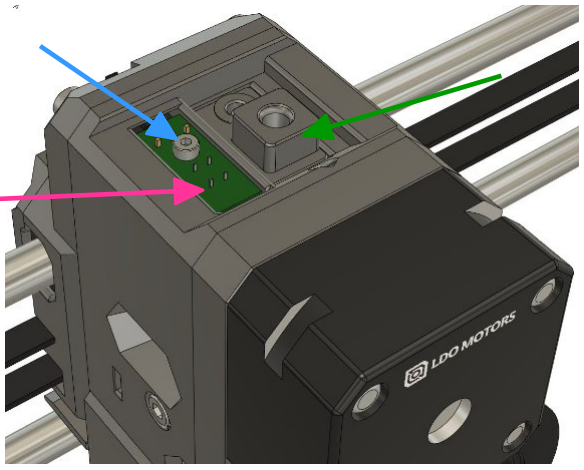
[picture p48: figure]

8. If you are using the PTFE mount option 2 with the E3D collet (e_fs_adapter_mmu2s_e3d) then install the collet in the part. After this, skip the next step and go directly to step 10

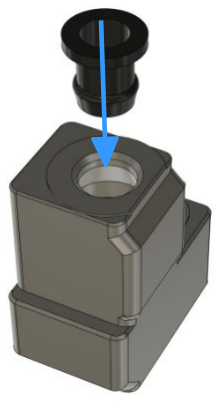
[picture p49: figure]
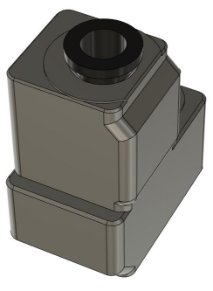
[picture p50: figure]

9. If you are using the PTFE mount option 1 with the Prusa hardware, then first screw the Festo coupler into the Prusa part. To remove the brass insert, use the Festo coupler as a lever and force it to the sides, repeat until the insert gets loose. Then unscrew the Festo coupler and press the brass insert in the e_fs_adapter_mmu2s_prusa with a vice or a plier wrench.

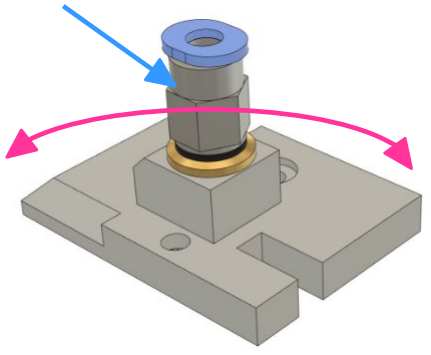
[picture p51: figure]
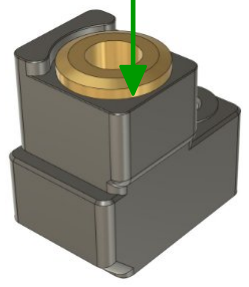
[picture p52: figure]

10. Insert the e_fs_adapter_mmu2s_xxx inside the extruder body (we use the option 1 Prusa as example). You do not need to care of the little lever previously used for the filament sensor, the adapter has space for it)

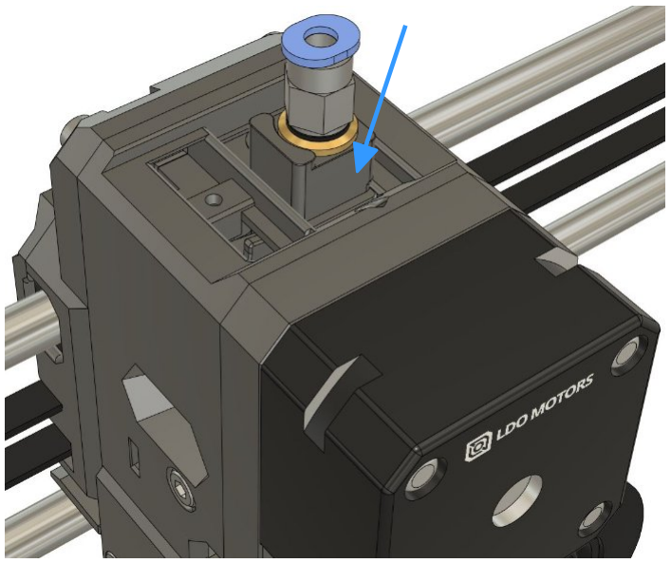
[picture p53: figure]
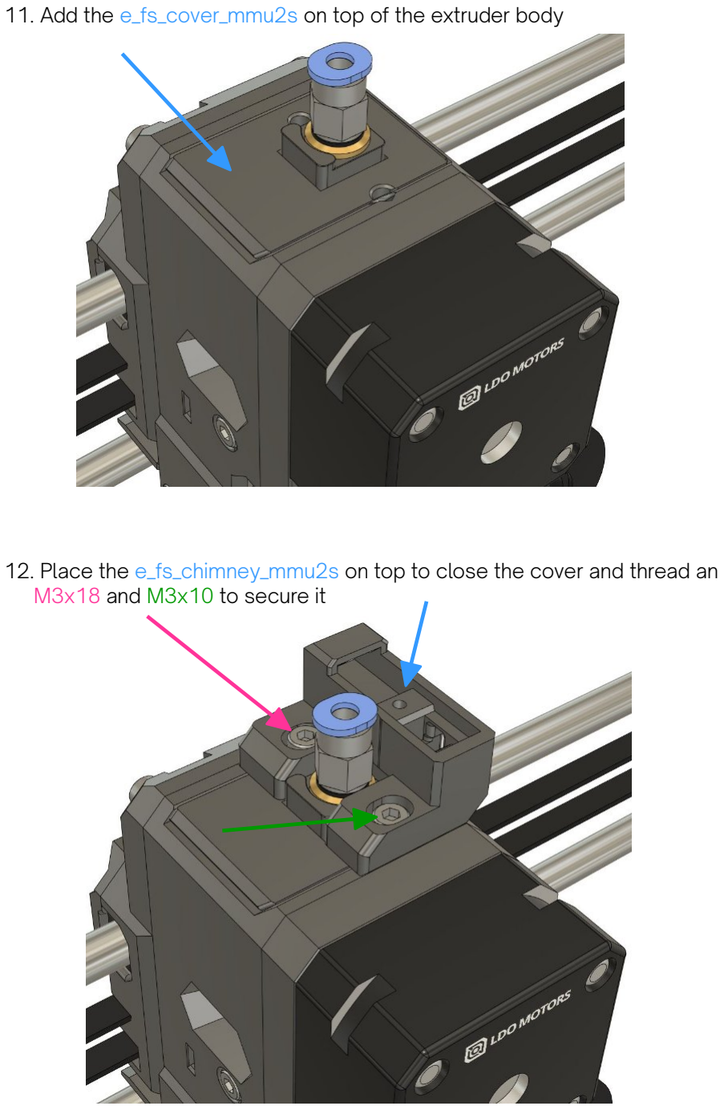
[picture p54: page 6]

11. Add the e_fs_cover_mmu2s on top of the extruder body
12. Place the e_fs_chimney_mmu2s on top to close the cover and thread an M3x18 and M3x10 to secure it

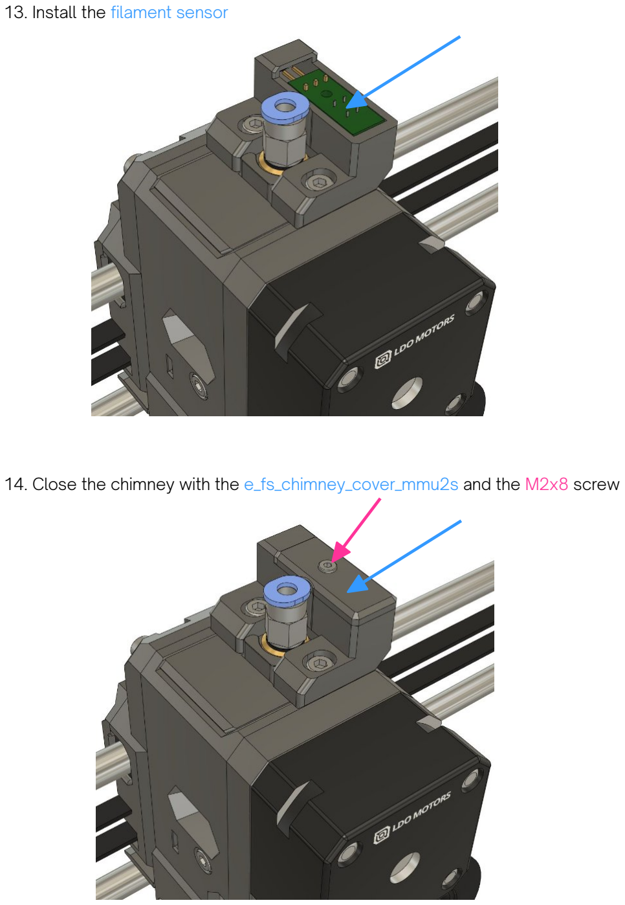
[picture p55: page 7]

13. Install the filament sensor
14. Close the chimney with the e_fs_chimney_cover_mmu2s and the M2x8 screw

15. Add the lever e_fs_lever_mmu2s on the side and secure it with an M3x14 screw

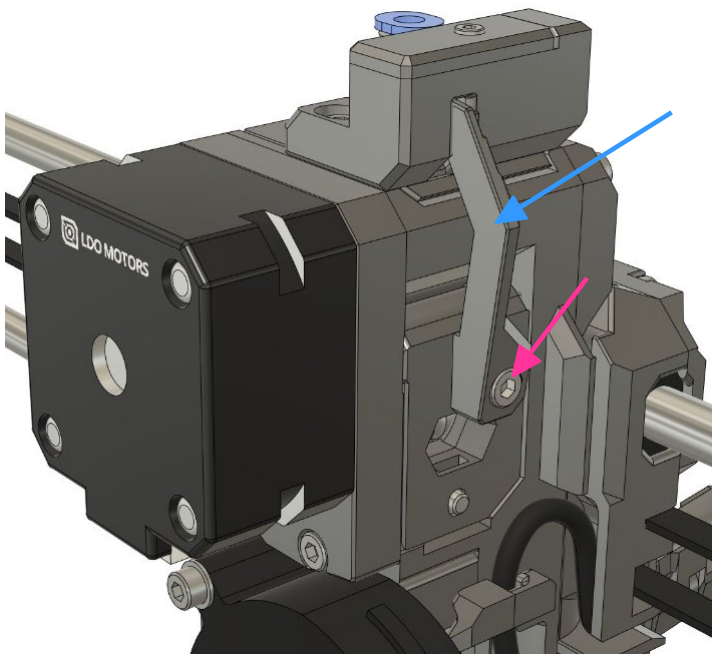
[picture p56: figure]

16. Insert the PTFE inside the Prusa coupler or E3D collet. If you are using the option 2 with E3D collet, lock the PTFE in place with e_fs_adapter_mmu2s_e3d_clip

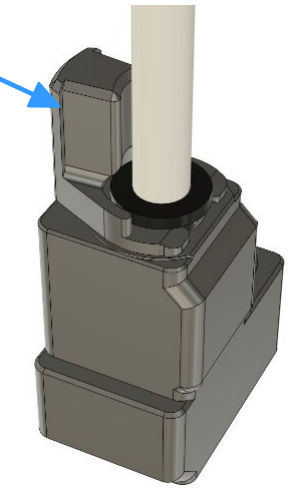
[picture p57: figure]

17. Follow the Preflight Check & Calibration guide from Prusa : https://help.prusa3d.com/guide/8-preflight-check-calibration_219068 . Note that the filament sensor calibration works the same way as the Prusa version.

Happy Printing:)

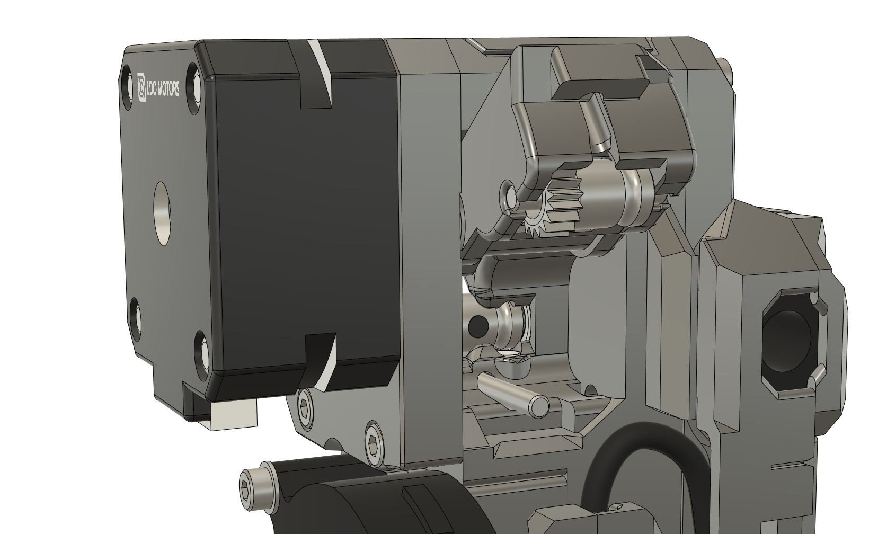
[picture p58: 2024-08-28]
extra/images/idler_print_gear_view.jpg

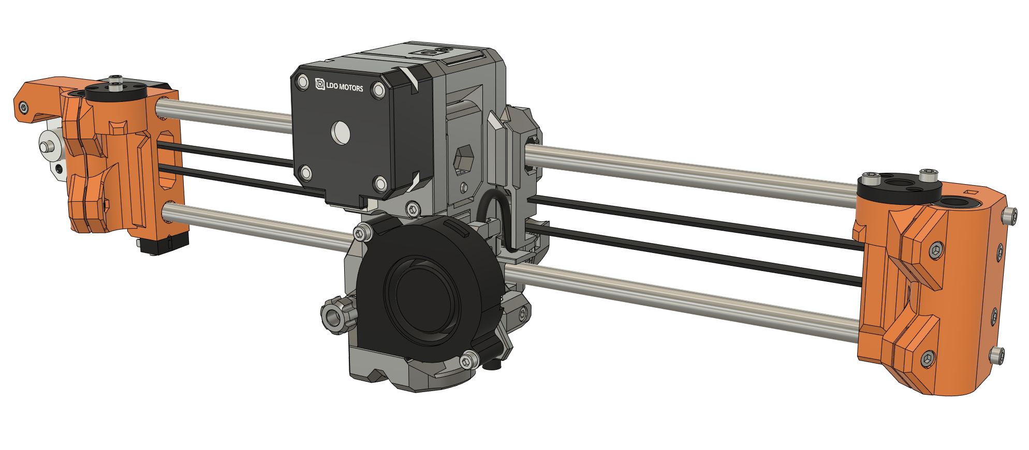
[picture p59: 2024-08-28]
extra/images/assembly_02.jpg

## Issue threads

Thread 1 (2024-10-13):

MK3.5(S) compatibility test

gregsaun, 2024-10-13:
If someone has a MK3.5(S) and is whiling to help the project we would be interested to test the BearExxa V2 with Prusa firmware.

If you don't want to change your MK3.5(S) extruder and X axis you may still help us by answering the questions bellow.

**Points to check:**
  1. We can modify the e-step value
  2. We can save the e-step with a gcode command or LCD menu
  4. We can calibrate the thermal model for the hotend
  5. We can disable fan hotend speed regulation (alt fan feature on MK3S)
  6. We can set the Z length (alternatives are possible for this)
  7. Other?

Thank you in advance ❤️

Killajoedotcom, 2024-10-15:
Greg, I was just looking into refreshing a well-loved MK3.5S+. Very timely. If there is something I can do to help, please reach out to me.

gregsaun, 2024-10-15:
Oh that's awesome, thanks!

I found that a lot of those settings can be set here :
https://help.prusa3d.com/article/experimental-settings-mk4-s-mk3-9-s-mk3-5-s-xl-mini_264396

That's a very good news!

A few questions for you:
1. Do you have a Revo hotend on your MK3.5S?
2. Can you find something about the thermal calibration of the hotend or hotend PID in the menu?
3. Could you tell me what extruder steps are set by default? I can then calculate the default micro stepping value
4. By any chances, do you have the hardware to build the beta version of BearExxa V2 (check the [BOM here](/doc/bom.md))?

Thank you in advance!

Killajoedotcom, 2024-10-15:
I was told the printer needed to be flashed with updated firmware again. I'll get to it this week.

1. It does have the E3D Revo six installed. I do have the Revo micro heatsink floating around as well.
2. TBD
3. TBD
4. I do have the things for the beta BOM on hand. Only thing I need to double check is the number of magnets in stock.

Killajoedotcom, 2024-10-18:
Greg, I'm sorry. I have been misreading your post for two days now. You're looking for a MK3.5, whereas I was reading MK3.

gregsaun, 2024-10-18:
No worries, all good, thanks anyway to have proposed your help. All those x.5, .9, S, S+ name can be very confusing sometimes. You are not the first neither the last!

Otherwise, the BearExxa V2 beta supports MK3S+. If you encounter issues, do not hesitate to open a new issue and I will help you.

Killajoedotcom, 2024-10-18:
Will do. Working on collecting the things to make it a bear with BearExxa V2. Printing parts now.

gregsaun, 2024-10-18:
@Killajoedotcom good for you if I delete all your comments to keep this issue clean?

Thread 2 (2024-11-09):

Download does not exist

Starlynk1, 2024-11-09:
Tried using the download link and it says there is nothing there. Checked for releases as that is where the link is pointing to and no releases. In the process of upgrading from the original Bear 2.0 frame (mk2.5s) and want to do all of it including the v2 exxa.

gregsaun, 2024-11-10:
Hello, I'm still working on building the repository for the release. This is why there is no release yet and the links are not working. Once the release will be set the link will work. The STL will not change until the release but some documentation and text in the repository will.

I'm closing this one, please reopen if not clear enough.

Closed 2024-11-10.

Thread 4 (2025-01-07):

Support for E3D v6 hotend?

luanft, 2025-01-07:
Hi,

I like the gearbox in this version. Unfortunately, it looks like the BearExxa-v2 doesn't support the E3D-v6 hotend. Do you have any plan to support it?

Thank you

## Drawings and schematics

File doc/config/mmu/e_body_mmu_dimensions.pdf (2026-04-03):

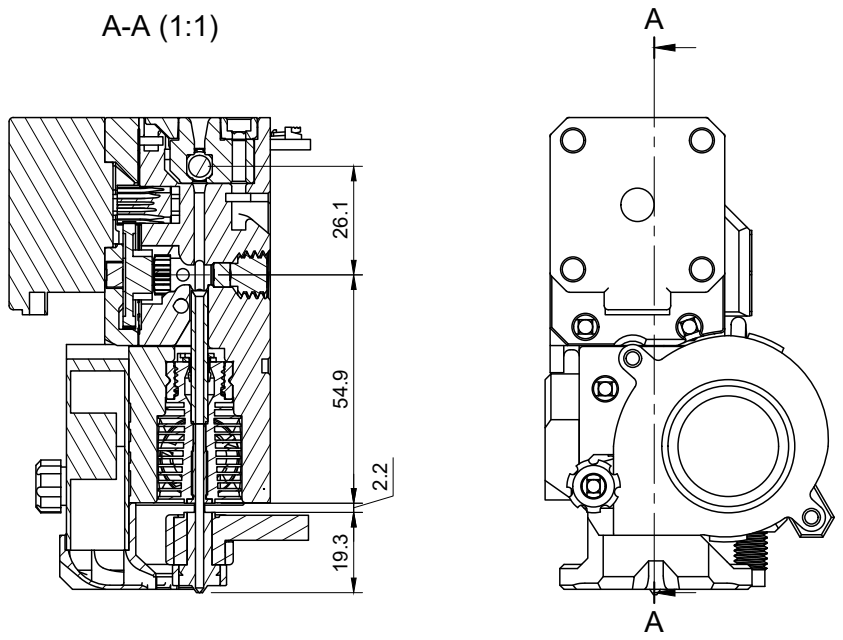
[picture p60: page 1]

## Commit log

2024-08-16 Readme: credit link fan duct knob
2024-08-16 Readme: non, print settings, config titles
2024-08-23 Readme: print quality
2024-08-23 Readme: print quality typos and sentences
2024-08-28 add print settings
2024-08-28 Add bom
2024-08-28 BOM: title level
2024-08-28 BOM: fix number of motor for extruder
2024-08-28 readme: add link to BOM and print settings
2024-08-29 Create quick assembly guide readme
2024-08-29 Create quick assembly guide images folder
2024-08-29 add wuuvk assembly guides images
2024-08-29 Quick assembly fix link
2024-08-29 quick assembly fix links
2024-08-29 README.md assembly guide link and add disclaimer
2024-09-01 Readme: add section for Printed Parts, Community and Support My Work
2024-09-05 Nicer quick assembly guide
2024-09-05 Quick assembly guide: fix links
2024-09-05 Quick assembly guide: make zip downlable
2024-09-09 Design goals: add TOC and add FAQ about Revo Micro heatsink
2024-09-09 Design goals: add FAQ about single hotend support
2024-09-12 Design goals: improve fast insert FAQ description
2024-09-17 Print settings: better warning and caution
2024-09-17 Quick assembly guide: better tip visualisation
2024-09-17 Print settings: add caution about high flow.material
2024-09-23 Create cad folder structure
2024-10-04 add folder structure for printed parts
2024-10-04 Design goals: improve readability. add more motor and weight details.
2024-10-04 Design goals: typo. improve readability of print quality
2024-10-05 simpler printed part folder structure
2024-10-08 add CAD and STL
    [e_bearing_screw.stl, e_body.stl, e_cover.stl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]
2024-10-08 Design goals: typo and extra info for hotend
2024-10-11 add optional parts
    [e3d_collet_clip.f3d, e3d_collet_clip.step, e3d_collet_clip.stl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]
2024-10-12 Readme: shorter bom intro text
2024-10-13 doc/config has now a slicer filder in case of
2024-10-14 readme: replace download links by button
2024-10-14 linknto download button for all optional parts. improve EM warning
2024-10-17 Bom: moved belt to X axis table. split hotend in several parts. add info for idler/pulley.
2024-10-17 typo. fix HeaterCore voltage for MK2
2024-10-19 quick assembly guide: fix link and improve steps
2024-10-19 readme: rename download button
2024-10-19 readme: replace printed part section by download
2024-10-19 quick assembly guide: now use the download button for the config from the main readme
2024-10-20 add Klipper config
2024-10-20 config: use same klipper thermistor as recommended by E3D. Add generic values
2024-10-21 bom: add info for which parts is reused from Prusa
2024-11-10 switch file format to unix
2024-11-11 bom: add missinf nylock
2024-11-30 Update README.md
    Ensure Klipper configurations are more explicit.
2024-12-15 Firmware config: X axis current pushed to 0.5A
2024-12-24 add wiring step
2024-12-24 improve doc for downloading the printed parts
